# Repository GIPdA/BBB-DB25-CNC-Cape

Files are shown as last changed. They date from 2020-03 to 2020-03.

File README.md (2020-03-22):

# BBB DB25 CNC Cape
###### Simple Machinekit CNC Cape for Beaglebone Black

--

### /!\ NOT TESTED YET, stay tuned /!\

You'll find here the project files for a simple CNC-oriented Beaglebone Black Cape for a Machinekit setup.

This cape breaks out most of the 'free' I/Os of the BBB:

- 17 with 5V level shifters capable of up to 32mA source/sink (TI SN74LVC1T45) ;
- 17 directly routed to the BBB I/Os (3V3 max).

The 17 5V I/Os are routed to a 2-rows 26-pin header for HE10-like flat cable connection directly to a DB25 port (the 26th pin, not present on DB25 connectors, is 5V power).

The other 3V3 I/Os are here for possible expansions, **but they are not 5V tolerant!**

Project files are Circuit Studio. I may add Circuit Maker files when possible.

---
### BBB DB25 CNC Cape

I/O direction can be selected by the jumpers header, either with jumpers or by soldering a wire. Jumper present = input, otherwise it is an output. If either the 3V3 or the 5V supply of the level shifter is not present, the outputs are high impedance and there is no pull resistors.

The extension connector has 5V and 3V3 power from the BBB. The 2 extra pads next to the extension connector can be manually wired to P9-41 and P9-42 (red dotted lines on the image below) if you want 2 extra I/Os on that connector.

The Cape can be assembled by JLCPCB SMT service. Use the files in ```BBB DB25 CNC Cape/Fab```. Only the bottom side has components. Headers and connectors cannot be assembled by JLCPCB, you'll need a 26-pin header and a 20-pin header for the extension if you want it.

For 5V power input, there is space to a 5.08mm screw terminal or a 3.5mm plug-in terminal. It powers the BBB and possible extensions.

Pads with the white silkscreen are the one used by the cape (including the extension).

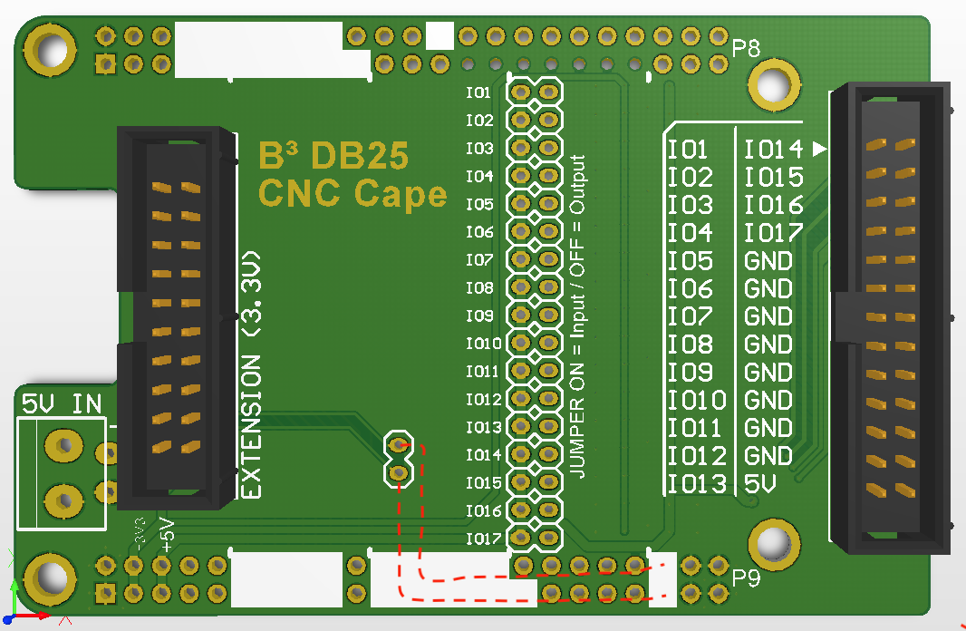
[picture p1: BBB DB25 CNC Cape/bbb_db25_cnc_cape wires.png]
BBB DB25 CNC Cape


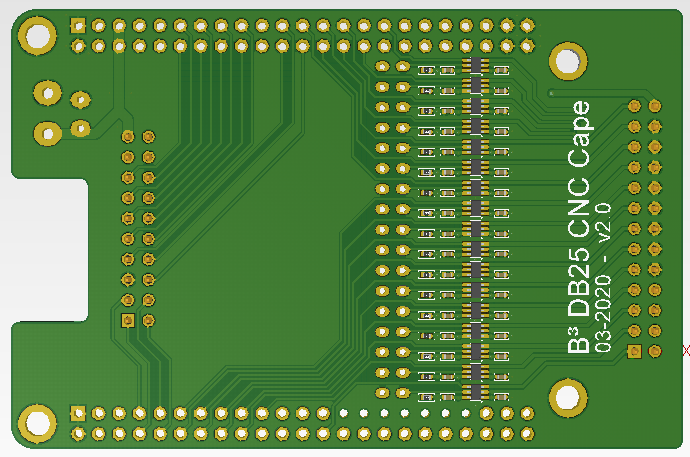
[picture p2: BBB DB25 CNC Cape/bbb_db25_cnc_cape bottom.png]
BBB DB25 CNC Cape


---
### BBB DB25 Terminals Extension

This is a PCB to break out the 26-pin HE10 connector to plug-in 3.5mm terminals (horizontal or vertical) in either one PCB or a stackup.

There is two rows of 4 connectors: top row is meant for step/dir outputs (2 I/Os + GND + 5V) with horizontal or vertical terminals. Bottom row is meant for limit switchs, enable and such, with vertical terminals.
The 5-pin terminal is linked to the encoder B input of the BBB.

The bottom row can be stacked up on another PCB to use horizontal terminals if needed (```bbb_db25_terminals_extension_top```).

Gerbers and other fab files are in folders ```bbb_db25_terminals_extension``` and ```bbb_db25_terminals_extension_top```.

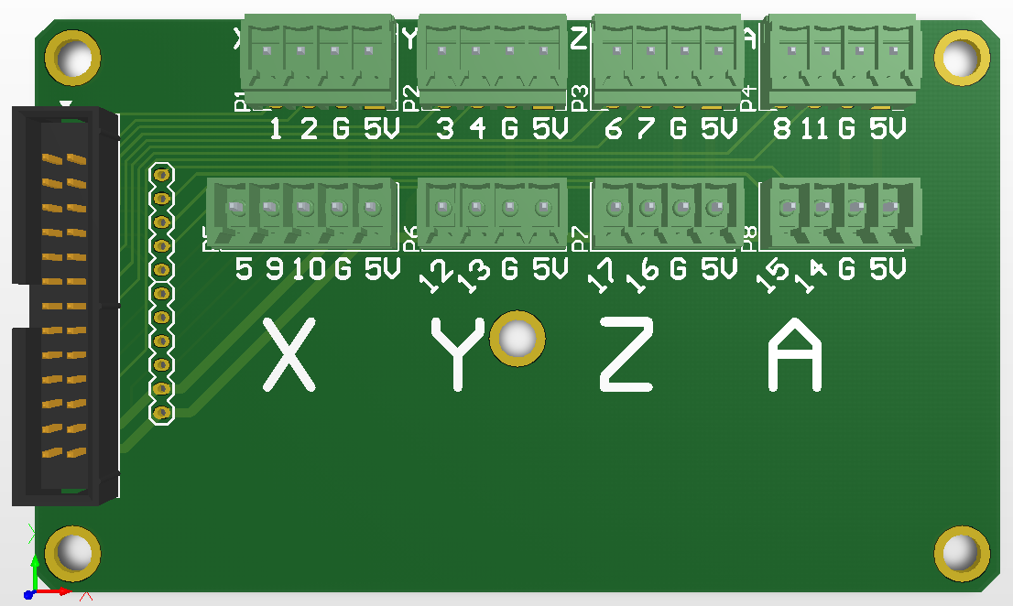
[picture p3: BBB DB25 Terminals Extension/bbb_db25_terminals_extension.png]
Terminals Extension


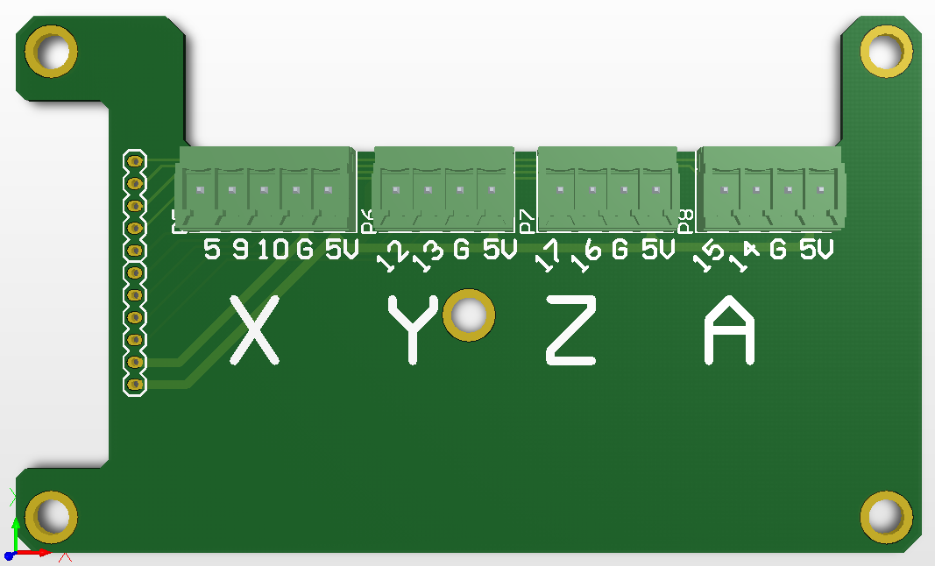
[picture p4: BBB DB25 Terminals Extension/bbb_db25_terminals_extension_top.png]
Terminals Extension Top


--
### Pinout tables

| DB25  | BBB I/O | HE10 Connector | |
|---|---|---|---|
| IO1 | P8_26 | 1 | |
| IO2 | P8_19 | 3 | |
| IO3 | P8_18 | 5 | |
| IO4 | P8_17 | 7 | |
| IO5 | P8_16 | 9 | Encoder 2 Index |
| IO6 | P8_15 | 11 | |
| IO7 | P8_14 | 13 | |
| IO8 | P8_13 | 15 | |
| IO9 | P8_12 | 17 | Encoder 2 A |
| IO10  | P8_11 | 19 | Encoder 2 B |
| IO11  | P9_23 | 21 | |
| IO12  | P9_26 | 23 | PRU 1-16 (in) |
| IO13  | P9_25 | 25 | PRU 0-7 |
| IO14  | P9_28 | 2 | PRU 0-3 |
| IO15  | P9_27 | 4 | PRU 0-5 |
| IO16  | P9_30 | 6 | PRU 0-2 |
| IO17  | P9_31 | 8 | PRU 0-0 |
| GND | GND | 10 | |
| GND | GND | 12 | |
| GND | GND | 14 | |
| GND | GND | 16 | |
| GND | GND | 18 | |
| GND | GND | 20 | |
| GND | GND | 22 | |
| GND | GND | 24 | |
| 5V | 5V | 26 | |

| | BBB I/O | Extension Connector |
|---|---|---|
| EXT1  | P8_8 | 1 |
| EXT2  | P8_10 | 2 |
| EXT3  | P8_7 | 3 |
| EXT4  | P8_9 | 4 |
| GND | GND | 5 |
| EXT5  | P9_24 | 6 |
| EXT6  | P9_22 | 7 |
| EXT7  | P9_21 | 8 |
| EXT8  | P9_18 | 9 |
| EXT9  | P9_17 | 10 |
| EXT10 | P9_16 | 11 |
| EXT11 | P9_15 | 12 |
| EXT12 | P9_14 | 13 |
| EXT13 | P9_13 | 14 |
| EXT14 | P9_12 | 15 |
| EXT15 | P9_11 | 16 |
| EXT16 | (P9_41) | 17 |
| EXT17 | (P9_42) | 18 |
| 5V | 5V | 19 |
| 3V3 | 3V3 | 20 |

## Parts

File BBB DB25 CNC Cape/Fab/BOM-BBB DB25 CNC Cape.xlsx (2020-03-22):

Designator | Comment | Footprint | LCSC Part #
CA1, CA2, CA3, CA4, CA5, CA6, CA7, CA8, CA9, CA10, CA11, CA12, CA13, CA14, CA15, CA16, CA17, CB1, CB2, CB3, CB4, CB5, CB6, CB7, CB8, CB9, CB10, CB11, CB12, CB13, CB14, CB15, CB16, CB17 | 100nF | 0402_C | C155422
RO1, RO2, RO3, RO4, RO5, RO6, RO7, RO8, RO9, RO10, RO11, RO12, RO13, RO14, RO15, RO16, RO17 | 10k | 0402_R | C25744
U1, U2, U3, U4, U5, U6, U7, U8, U9, U10, U11, U12, U13, U14, U15, U16, U17 |  | SOT65P210X110-6N | C9382

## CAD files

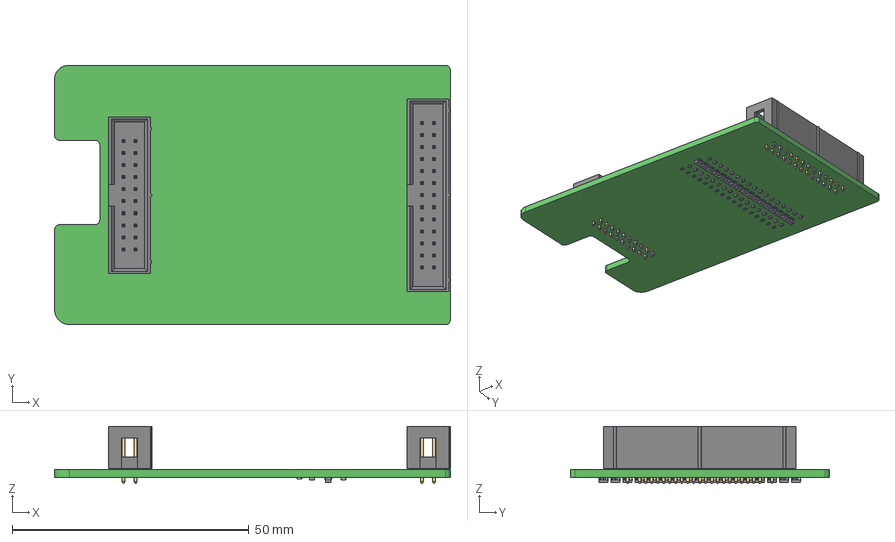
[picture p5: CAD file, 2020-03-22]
BBB DB25 CNC Cape/Default Configuration/Outputs/ExportSTEP/bbb_db25_cnc_cape.step
83.6 x 54.7 x 12.1 mm
Board
6120xx21621_PIN x 46
0402_resistor x 17
PinsArrayLR x 17
0402_cap x 34

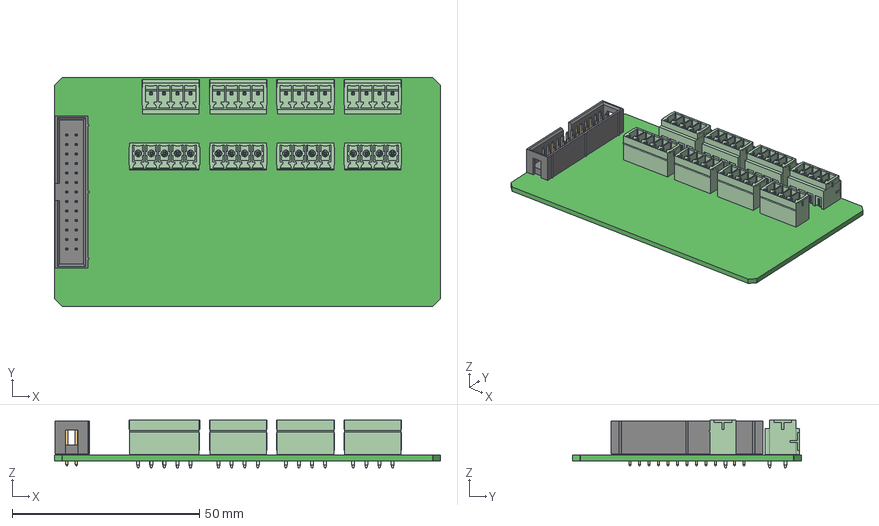
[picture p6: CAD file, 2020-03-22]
BBB DB25 Terminals Extension/bbb_db25_terminals_extension/Outputs/ExportSTEP/bbb_db25_terminals_extension.step
103.2 x 61.2 x 12.7 mm
Board
6913211000xx_PIN x 33
6120xx21621_PIN x 26
6913221100xx_PIN x 16

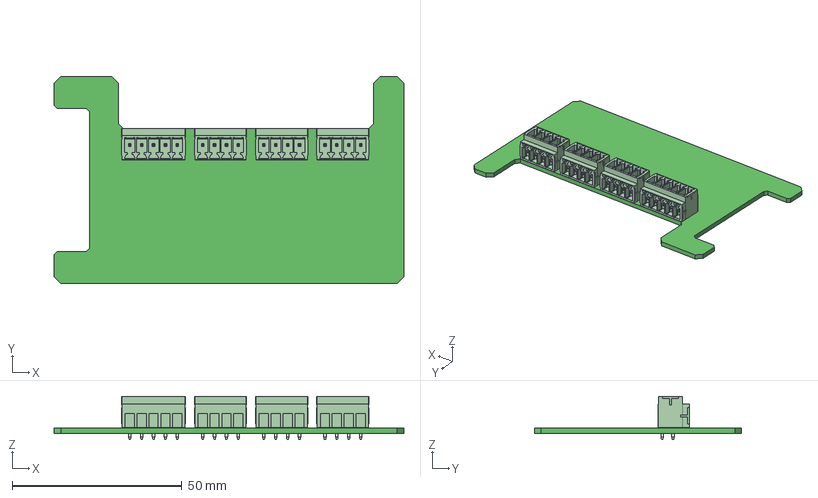
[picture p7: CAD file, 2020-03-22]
BBB DB25 Terminals Extension/bbb_db25_terminals_extension_top/Outputs/ExportSTEP/bbb_db25_terminals_extension_top.step
103.0 x 61.0 x 12.7 mm
Board
6913221100xx_PIN x 17
6913211000xx_PIN x 17

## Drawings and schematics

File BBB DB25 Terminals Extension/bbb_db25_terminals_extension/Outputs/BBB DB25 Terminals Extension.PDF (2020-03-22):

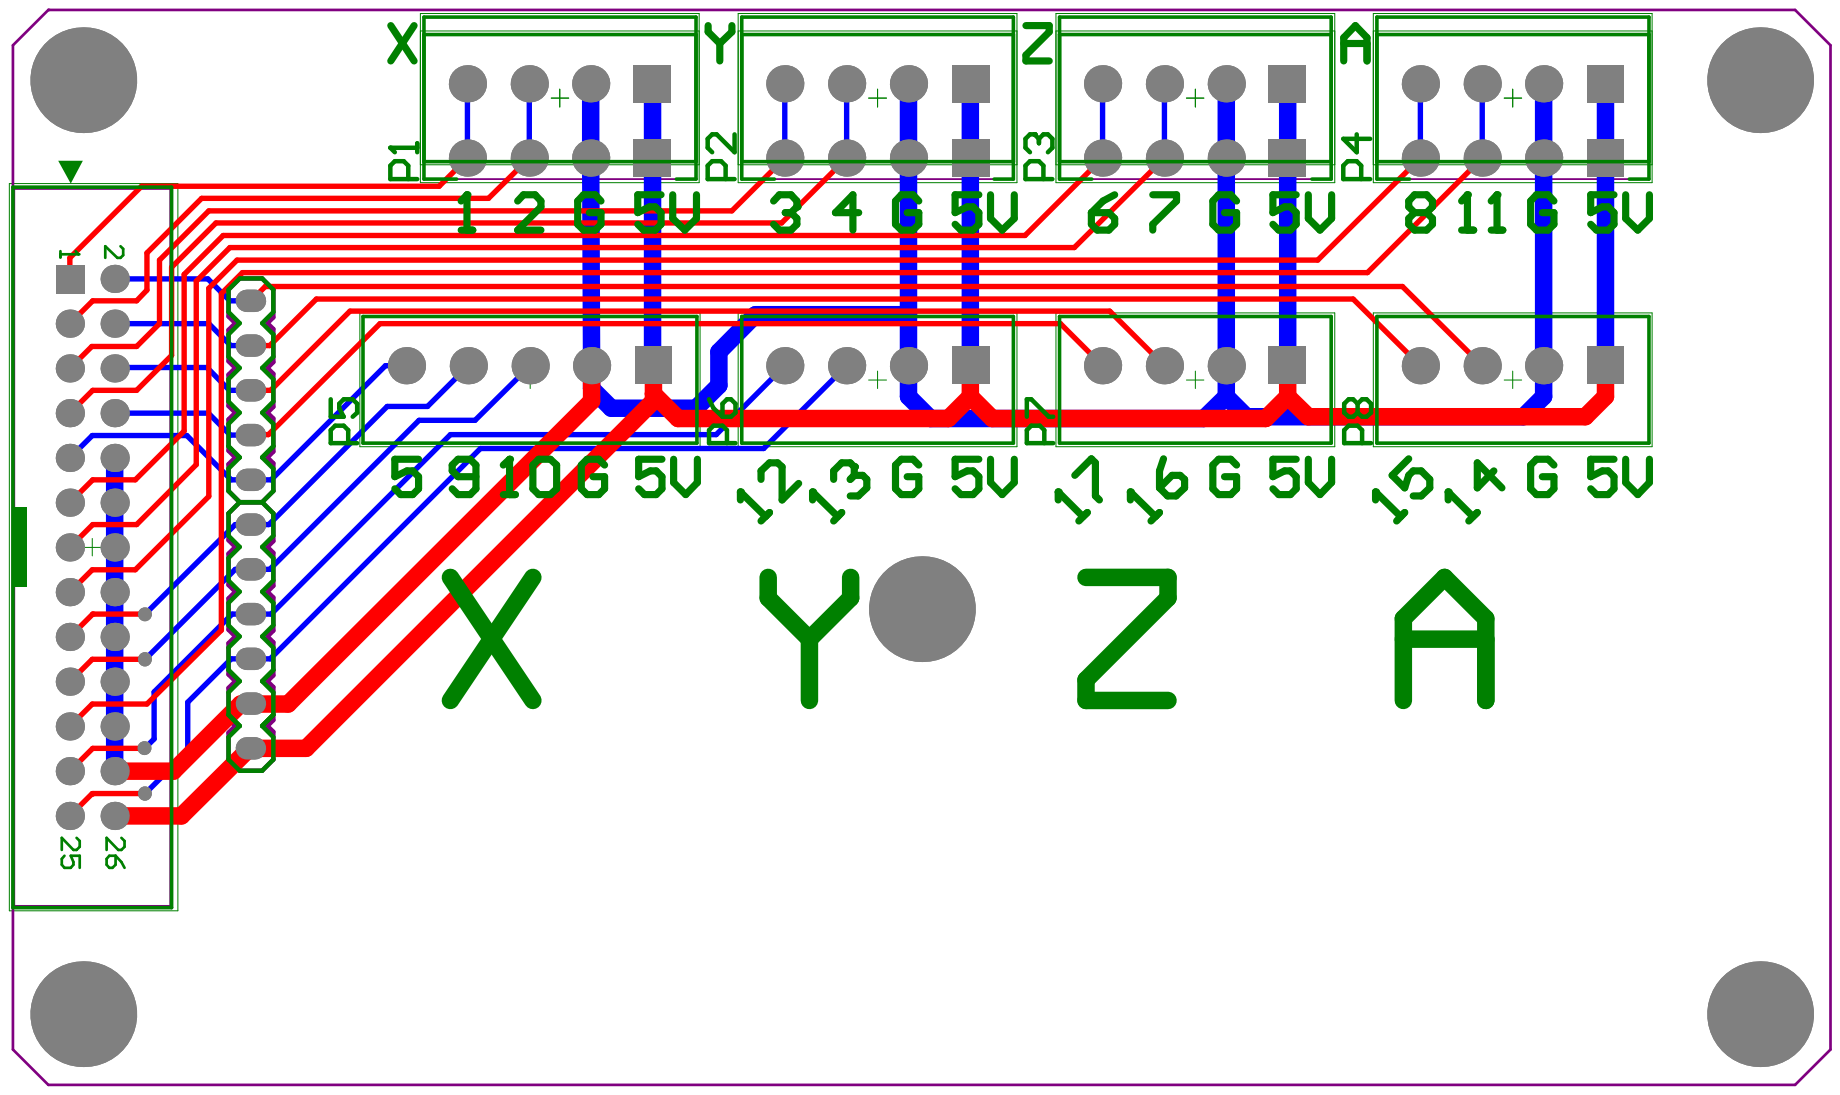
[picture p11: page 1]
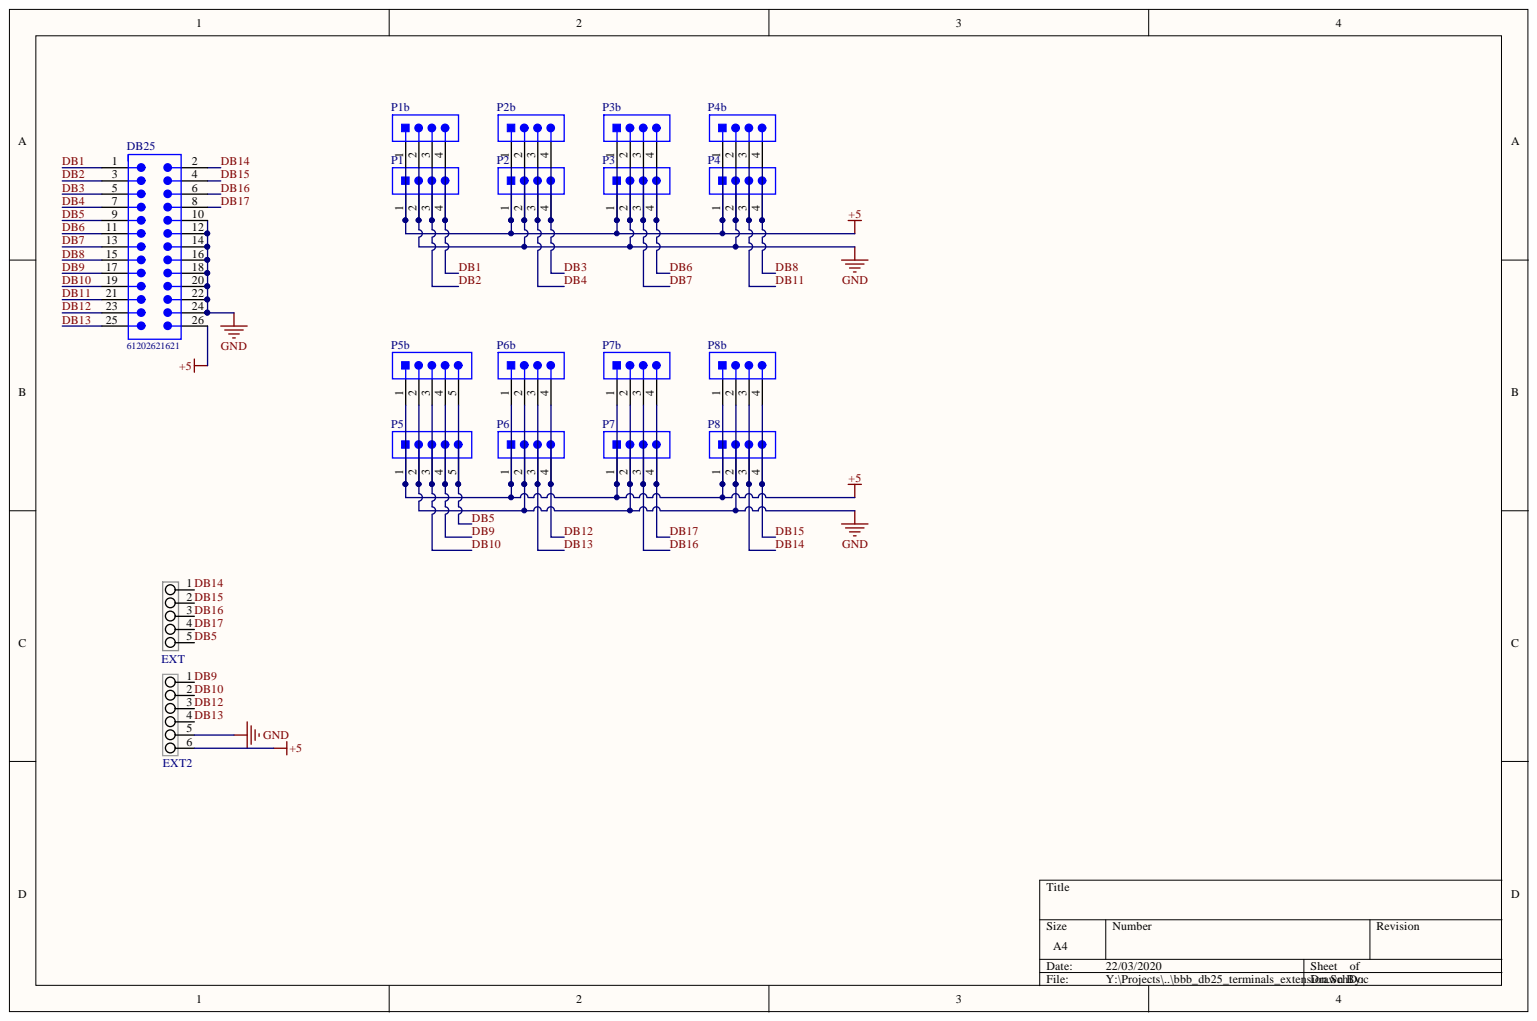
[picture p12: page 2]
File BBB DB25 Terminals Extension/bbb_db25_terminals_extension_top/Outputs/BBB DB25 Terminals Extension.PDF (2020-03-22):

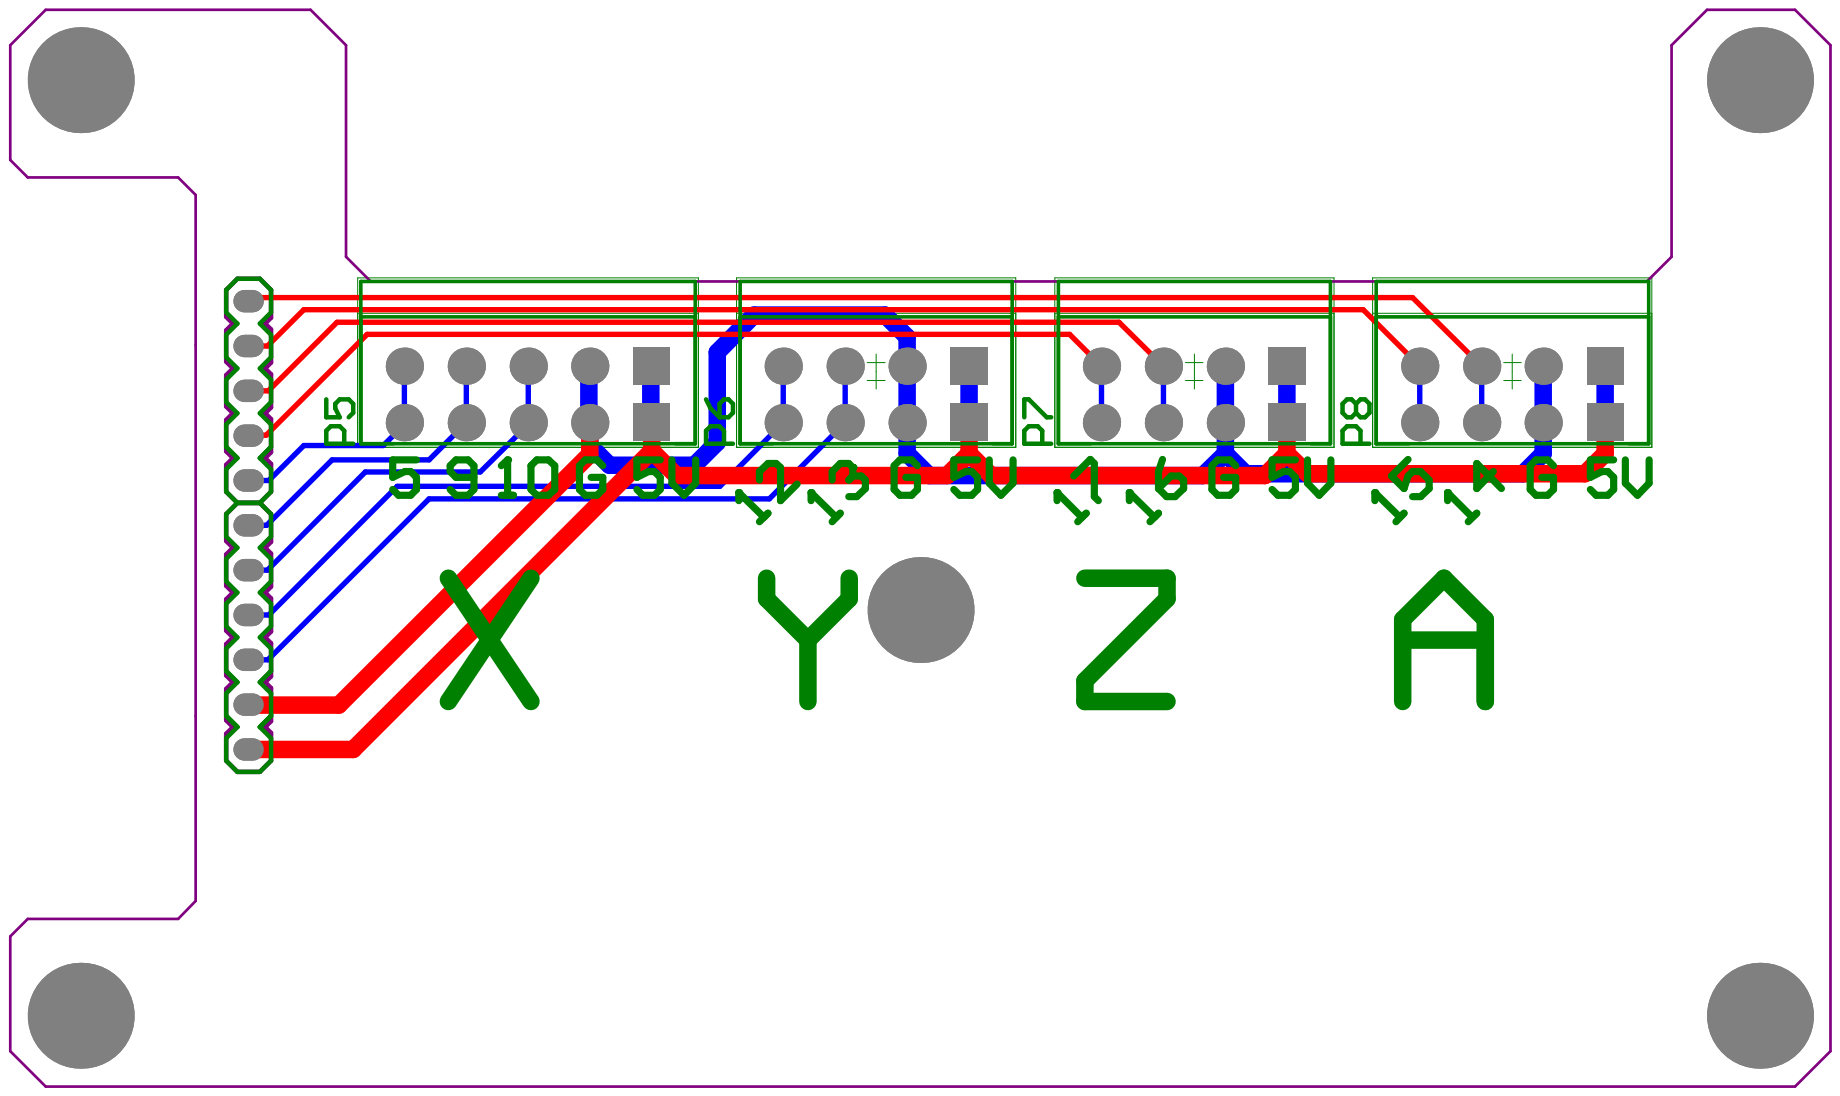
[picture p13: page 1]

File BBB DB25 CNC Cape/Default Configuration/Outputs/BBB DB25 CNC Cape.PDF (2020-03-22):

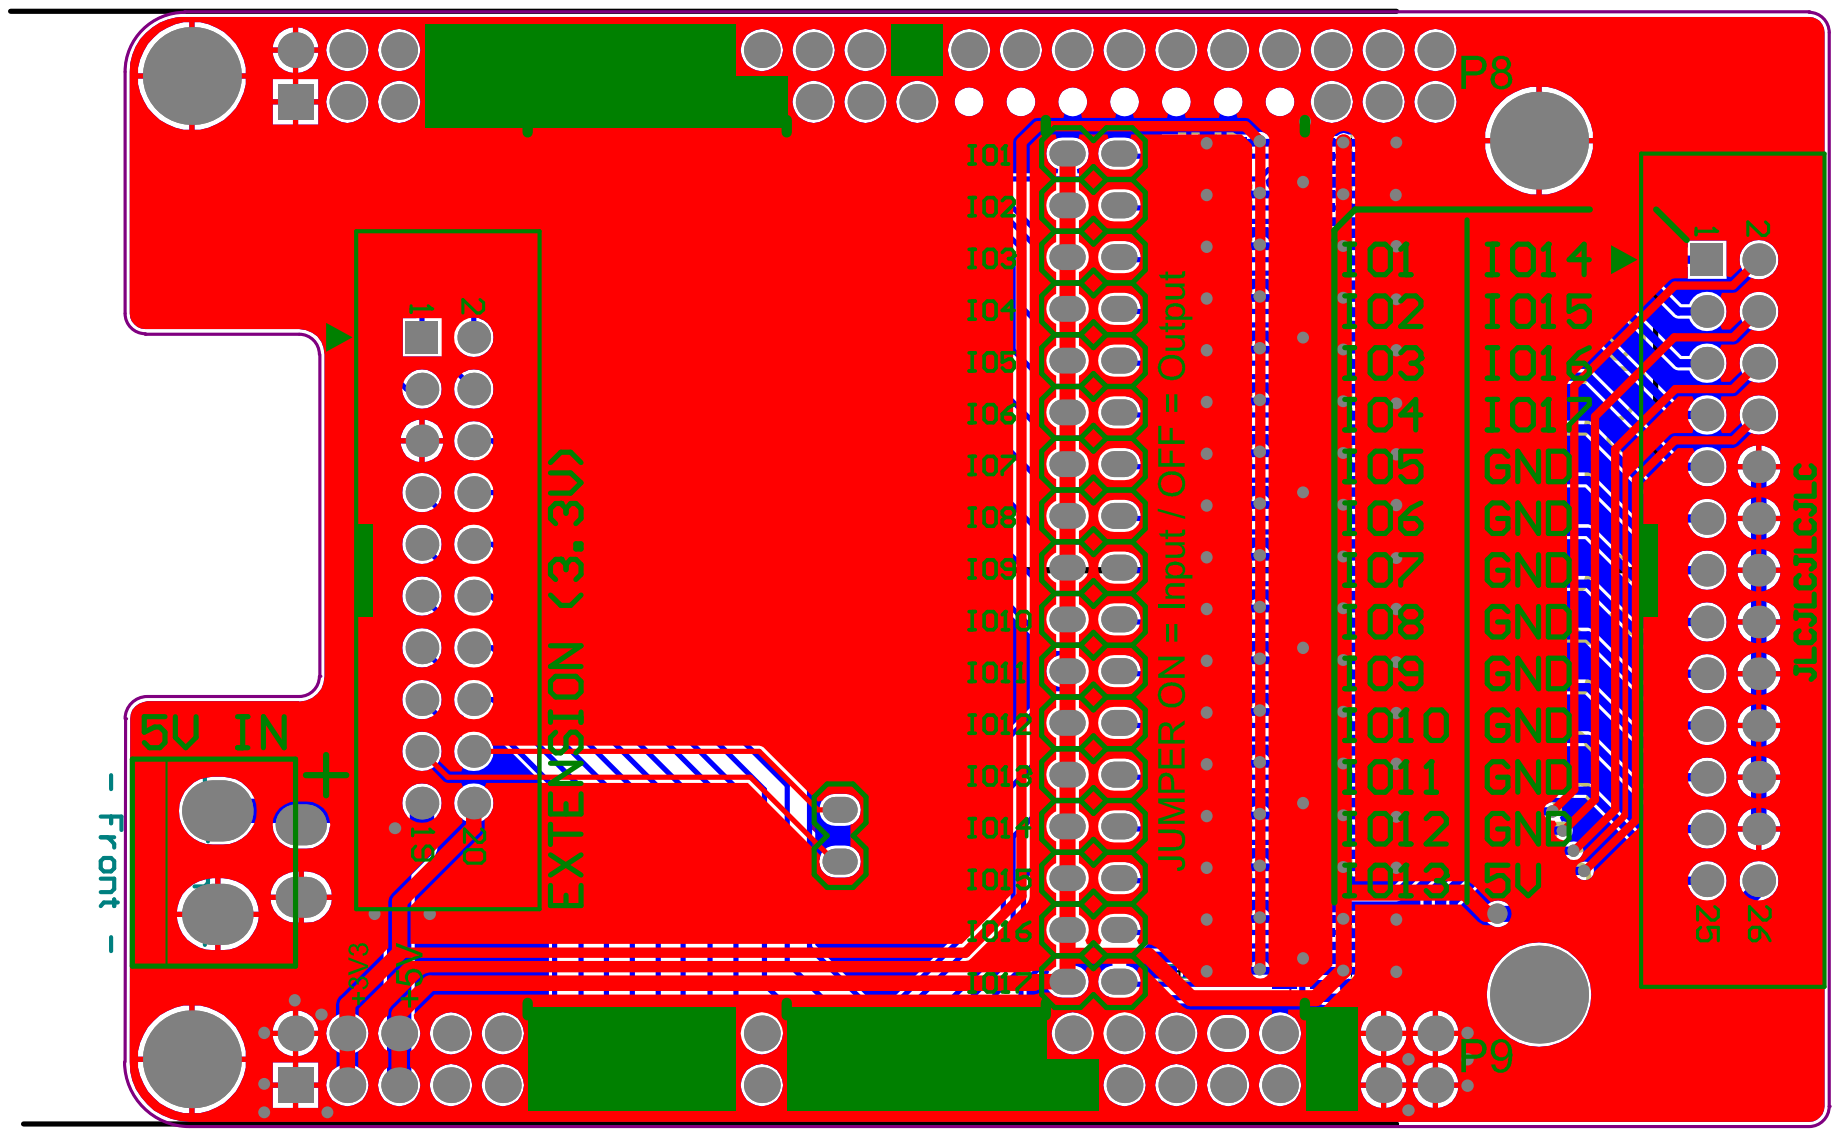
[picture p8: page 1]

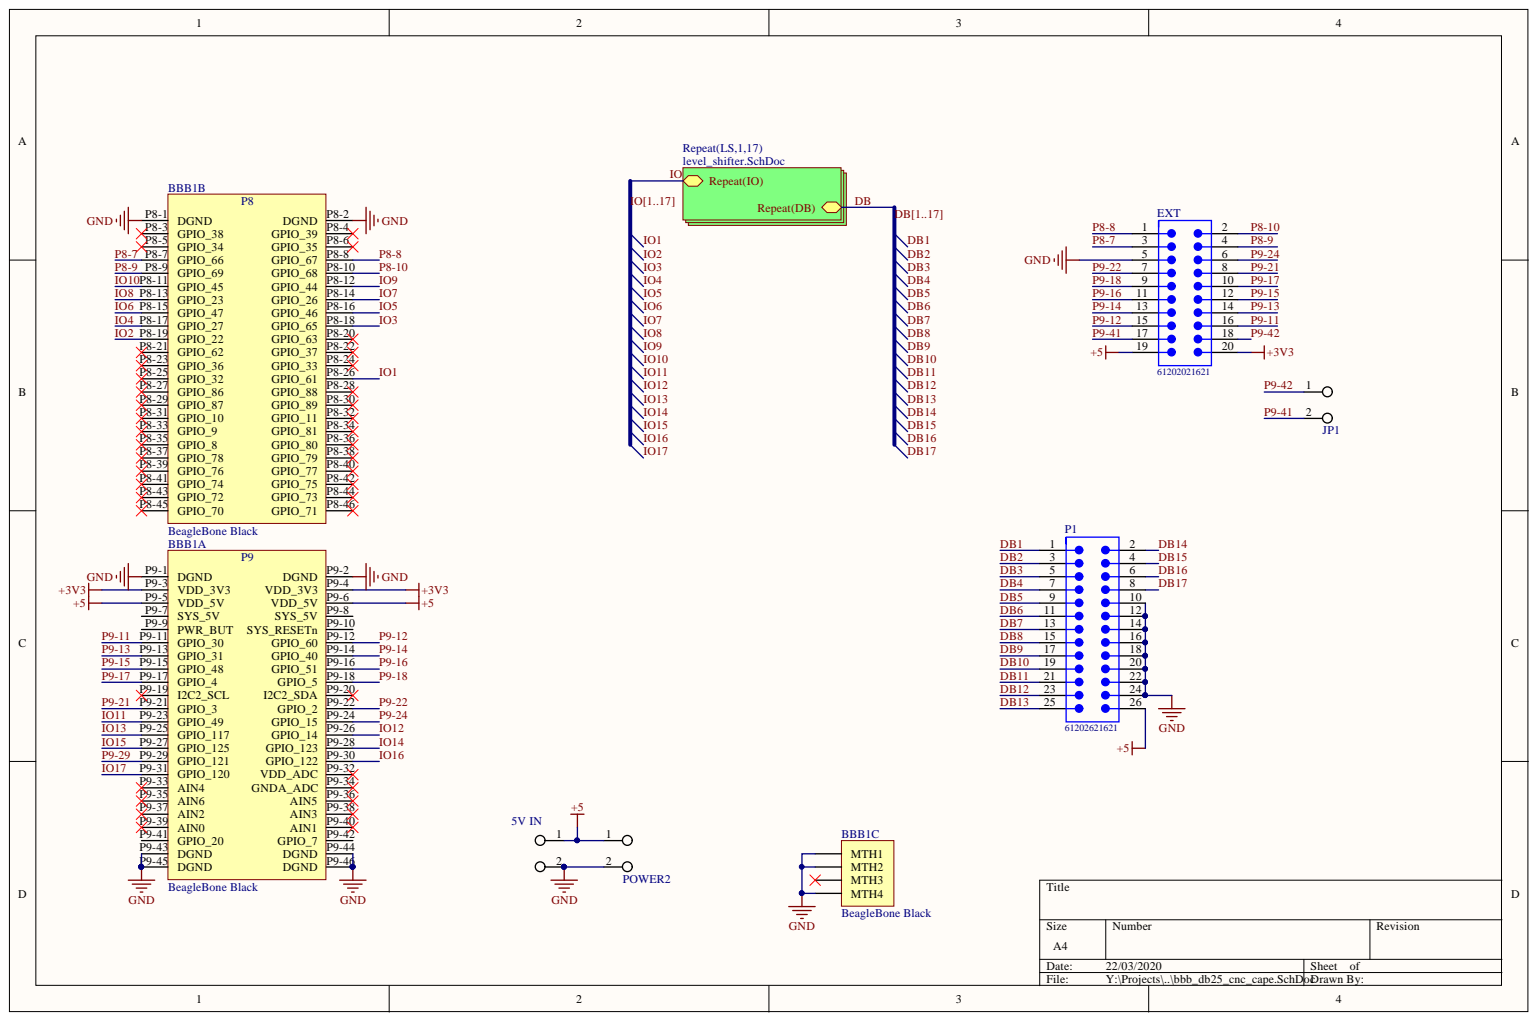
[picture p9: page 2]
Date:; Sheet of; File:; Y:\Projects\..\bbb_db25_cnc_cape.SchDocDrawn By:; DGND P9-1; DGND; VDD_3V3 P9-3; VDD_3V3; VDD_5V P9-5; VDD_5V; SYS_5V P9-7; SYS_5V; PWR_BUT P9-9; SYS_RESETn; GPIO_30 P9-11; GPIO_60; GPIO_31 P9-13; GPIO_40; GPIO_48 P9-15; GPIO_51; GPIO_4 P9-17; GPIO_5; I2C2_SCL P9-19; I2C2_SDA; GPIO_3 P9-21; GPIO_2; GPIO_49 P9-23; GPIO_15; GPIO_117 P9-25; GPIO_14; GPIO_125 P9-27; GPIO_123; GPIO_121 P9-29; GPIO_122; GPIO_120 P9-31; VDD_ADC; AIN4 P9-33; GNDA_ADC; AIN6 P9-35; AIN5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

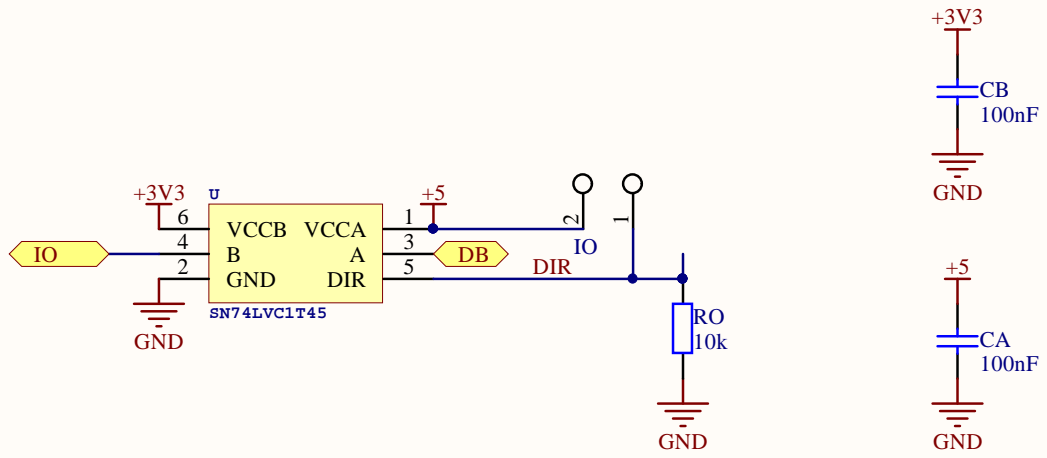
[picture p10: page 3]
Sheet o; PICA02 COCA; PICB02 COCB; PIIO02; PIIO01 COIO; PIIO02 PIU01; PIIO01; PIRO01 PIU05; NLDIR
